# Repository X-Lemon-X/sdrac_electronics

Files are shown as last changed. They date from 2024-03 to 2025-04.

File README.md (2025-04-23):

 
# SDRAC electronic design
This repository contains the psb schematics and designs of the SDRAC board.

## SDRACboard
- Supply voltage 12-48V (9-55V)
- the board has a 5V/2A on board regualator, to power the board and peripherals
- USB-C for programming and reading data
- ST-wire pins for programming and debugging
- 3 bit hardware address CID0, CID1, CID2
- 6 pin JS connector for IO-appliacitons, with analog, UART, Timers, 5V and GND
- 2x 4 pin Molex connectors for CAN bus
- 2x 6 pin Molex connectors for I2C magnetic encoder
- 2x 2 pin Molex connectors for external temperature sensors (ntc termistors)
- 1x 4 pin Molex connector for stepper motor
- 1x 4 pin connector for external steper motor driver
- 1x Screw terminal for external steper motor driver power
- XT30-M, XT30-F  connectors for input and output power

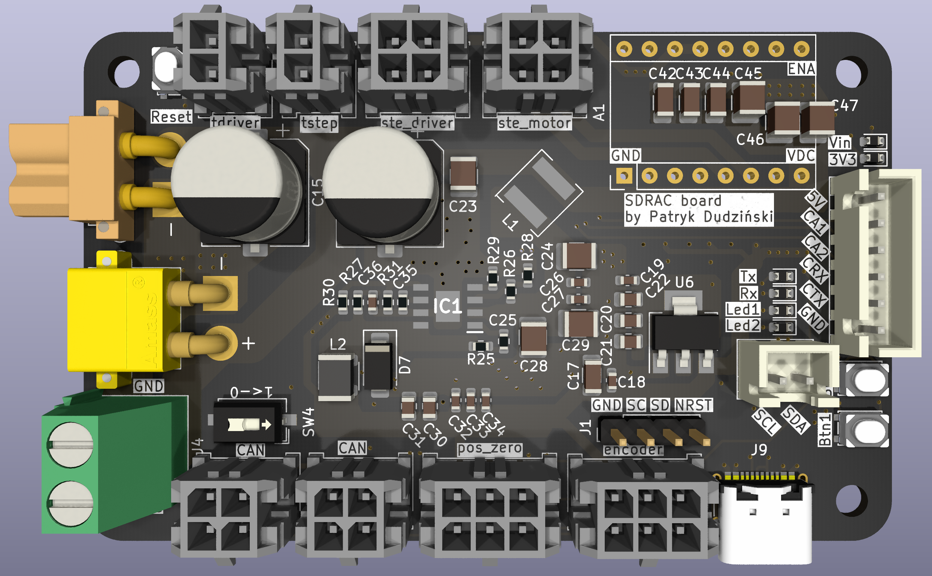
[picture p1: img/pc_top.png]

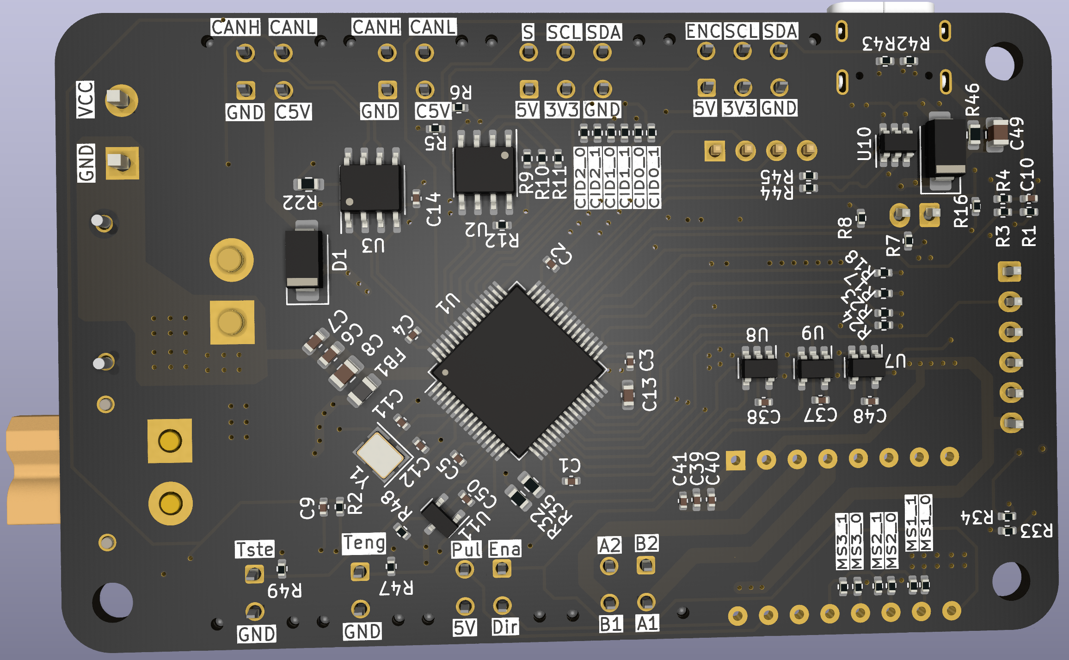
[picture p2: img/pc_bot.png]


## Schematics
The schematics are made in KiCad.

## Assembly
Manual assembly takes about 2 hours, with stemple and hot air station.

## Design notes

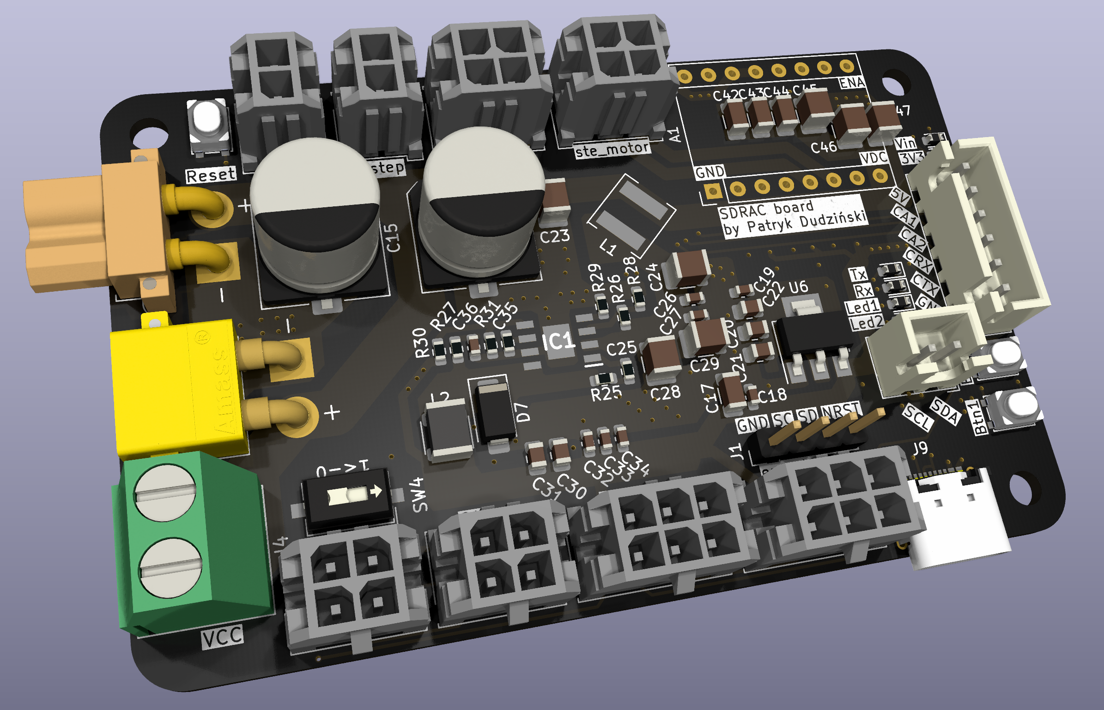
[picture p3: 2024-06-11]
img/front.png

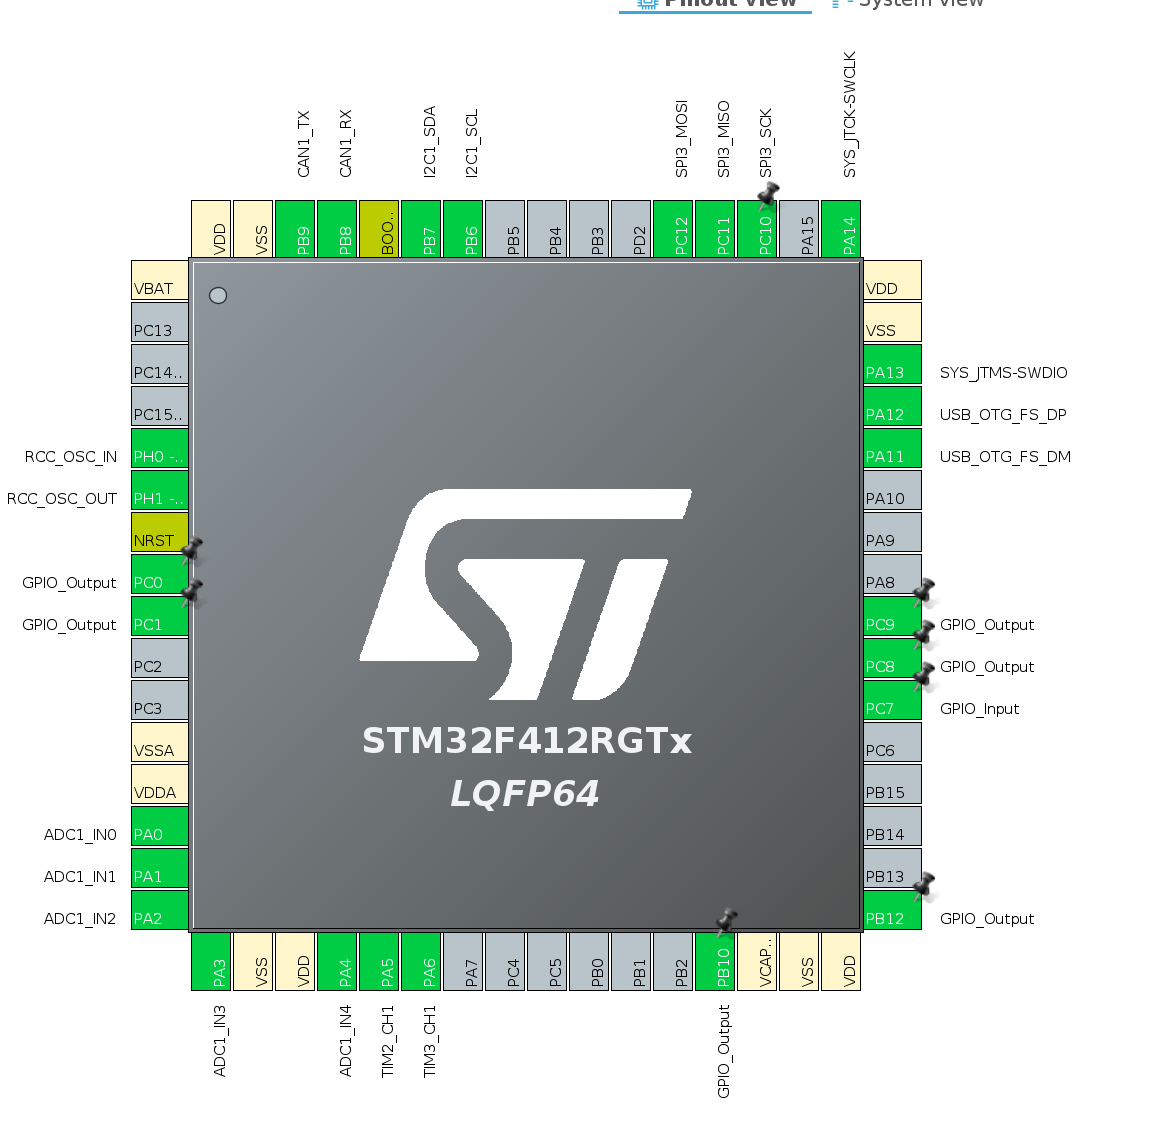
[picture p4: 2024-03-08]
datasheets/stm_cube_uc_image.png

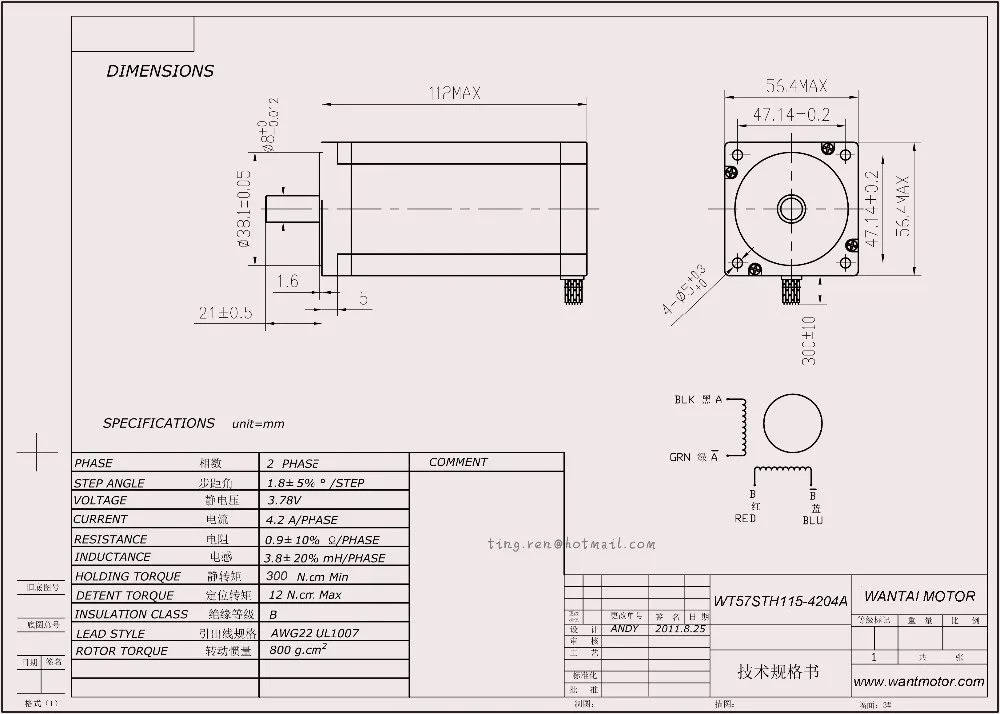
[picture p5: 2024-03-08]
datasheets/steper_motor_big.webp

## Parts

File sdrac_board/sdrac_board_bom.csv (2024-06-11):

Id | Designator | Footprint | Quantity | Designation | Supplier and ref
1 | R28 | R_0603_1608Metric | 1 | 86.6k
2 | U4,U5 | Molex_Micro-Fit_3.0_43045-0412_2x02_P3.00mm_Vertical | 2 | CAN
3 | R29 | R_0603_1608Metric | 1 | 60.4k
4 | U6 | SOT-223-3_TabPin2 | 1 | AZ1117-3.3
5 | J6 | AMASS_XT30PW-F_1x02_P2.50mm_Horizontal | 1 | Conn_01x02_Female
6 | J8 | Molex_Micro-Fit_3.0_43045-0412_2x02_P3.00mm_Vertical | 1 | STEPER_DRIVER_MOTOR_OUT
7 | SW4 | SW_DIP_SPSTx01_Slide_6.7x4.1mm_W6.73mm_P2.54mm_LowProfile_JPin | 1 | SW_DIP_x01
8 | D6 | D_0603_1608Metric | 1 | LED_TXD
9 | C16,C15 | CP_Elec_10x10.5 | 2 | 47u
10 | J5 | AMASS_XT30PW-M_1x02_P2.50mm_Horizontal | 1 | Conn_01x02_Male
11 | R30,R32 | R_0603_1608Metric | 2 | 43k
12 | C35 | R_0603_1608Metric | 1 | 0.033u
13 | C33,C18,C26,C32,C19 | C_0603_1608Metric | 5 | 100n
14 | C43,C44 | C_1206_3216Metric | 2 | 100n
15 | C47,C23,C29,C28,C46,C24,C45 | C_1210_3225Metric | 7 | 10u
16 | J12 | Molex_Micro-Fit_3.0_43045-0612_2x03_P3.00mm_Vertical | 1 | Pos_zero_sens
17 | D3 | D_0603_1608Metric | 1 | USR_LED1
18 | C25 | R_0603_1608Metric | 1 | 100n
19 | C17 | C_1206_3216Metric | 1 | 10u
20 | C34,C27 | C_0603_1608Metric | 2 | 1n
21 | SW2 | SW_SPST_PTS810 | 1 | NRST
22 | SW1 | SW_SPST_PTS810 | 1 | BOOT0
23 | C30,C21,C31,C22,C20,C8 | C_0805_2012Metric | 6 | 10u
24 | R26 | R_0603_1608Metric | 1 | 430k
25 | R31 | R_0603_1608Metric | 1 | 7.5k
26 | D7 | D_SMA | 1 | SS34
27 | SW3 | SW_SPST_PTS810 | 1 | USR_BTN
28 | H1,H2,H3 | MountingHole_3.2mm_M3_ISO7380 | 3 | MountingHole
29 | R27,R25 | R_0603_1608Metric | 2 | 5.1
30 | J11 | Molex_Micro-Fit_3.0_43045-0612_2x03_P3.00mm_Vertical | 1 | Mag_enc
31 | IC1 | SOIC127P600X170-9N | 1 | LMR16030PDDA
32 | J1 | PinHeader_1x04_P2.54mm_Vertical | 1 | SWD
33 | J9 | USB_C_Receptacle_G-Switch_GT-USB-7010ASV | 1 | USB_C_Receptacle_USB2.0
34 | J7 | Molex_Micro-Fit_3.0_43045-0412_2x02_P3.00mm_Vertical | 1 | STEPER_DRIVER_CONTROL
35 | L1 | L_6.3x6.3_H3 | 1 | 22u
36 | J3 | JST_XH_B6B-XH-A_1x06_P2.50mm_Vertical | 1 | INOUT
37 | D9 | D_0603_1608Metric | 1 | LV_PWR
38 | D8 | D_0603_1608Metric | 1 | HV_PWR
39 | D4 | D_0603_1608Metric | 1 | USR_LED2
40 | L2 | L_1812_4532Metric | 1 | 12u
41 | J4 | TerminalBlock_Phoenix_MKDS-1,5-2_1x02_P5.00mm_Horizontal | 1 | STEPER DRIVER VCC
42 | A1 | Pololu_Breakout-16_15.2x20.3mm | 1 | STEPER_MOTOR_BREAKOUT
43 | J10,J13 | Molex_Micro-Fit_3.0_43045-0212_2x01_P3.00mm_Vertical | 2 | Conn_01x02
44 | C36 | C_0603_1608Metric | 1 | 100p
45 | D5 | D_0603_1608Metric | 1 | LED_RXD
46 | C42 | C_1206_3216Metric | 1 | 1n
47 | J2 | JST_XH_B2B-XH-A_1x02_P2.50mm_Vertical | 1 | SYNCHRONIZER
48 | U3 | SOIC-8_3.9x4.9mm_P1.27mm | 1 | SN65HVD232
49 | R48,R47,R49 | R_0402_1005Metric | 3 | 100k
50 | R6,R8,R7,R5 | R_0402_1005Metric | 4 | 4k7
51 | C39,C40 | C_0402_1005Metric_Pad0.74x0.62mm_HandSolder | 2 | 100n
52 | U7,U9,U8 | SOT-23-5 | 3 | SN74LV1T34DBV
53 | U11 | SOT-23 | 1 | MCP9700AT-ETT
54 | R3,R23,R34,R1,R17,R24,R18 | R_0402_1005Metric | 7 | 1k
55 | R2,R4,R16,R19,R36,R13,R41,R20,R10,R15,R40,R39,R11,R12,R14,R33,R37,R9,R21,R38 | R_0402_1005Metric | 20 | 10k
56 | R45,R44 | R_0402_1005Metric | 2 | 22R
57 | R22 | R_0603_1608Metric | 1 | 120R
58 | U1 | LQFP-64_10x10mm_P0.5mm | 1 | STM32F412RGT6
59 | R43,R42 | R_0402_1005Metric | 2 | 5k1
60 | C2,C37,C9,C1,C50,C4,C14,C48,C5,C3,C38 | C_0402_1005Metric | 11 | 100n
61 | D2,D1 | D_SMA | 2 | D_Schottky
62 | R46 | R_0603_1608Metric | 1 | 33k
63 | C11,C12 | C_0402_1005Metric | 2 | 16p
64 | C6 | C_0603_1608Metric | 1 | 1u
65 | C49 | C_0805_2012Metric | 1 | 10n
66 | R35 | R_0603_1608Metric | 1 | 1k
67 | C41 | C_0402_1005Metric | 1 | 1n
68 | C7 | C_0603_1608Metric | 1 | 4.7u
69 | U10 | SOT-23-6 | 1 | USBLC6-2SC6
70 | C10 | C_0402_1005Metric | 1 | 4.7u
71 | C13 | C_0603_1608Metric | 1 | 2.2u
72 | Y1 | Crystal_SMD_3225-4Pin_3.2x2.5mm | 1 | 16MHz
73 | U2 | SOIC-8_3.9x4.9mm_P1.27mm | 1 | FM24CL16B
74 | FB1 | L_0805_2012Metric | 1 | FerriteBead

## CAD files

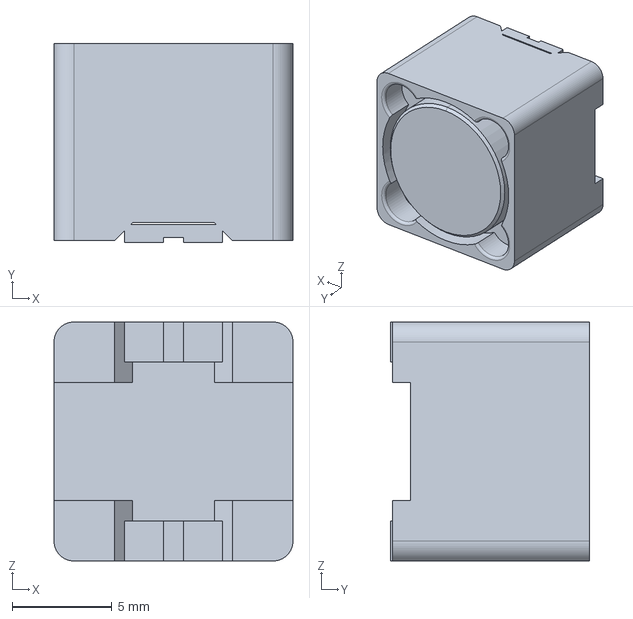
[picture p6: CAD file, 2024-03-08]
sdrac_board/3D models/SRR1210-471M.stp
12.0 x 10.0 x 12.0 mm

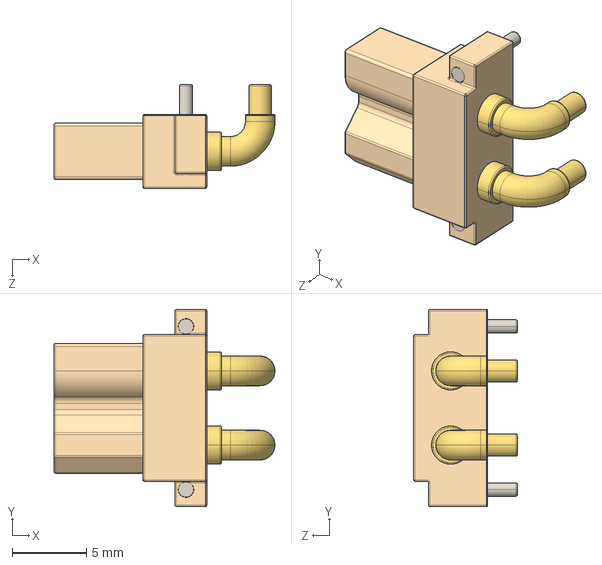
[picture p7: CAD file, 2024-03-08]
sdrac_board/3D models/XT30PW-F.STEP
14.9 x 13.3 x 7.00 mm

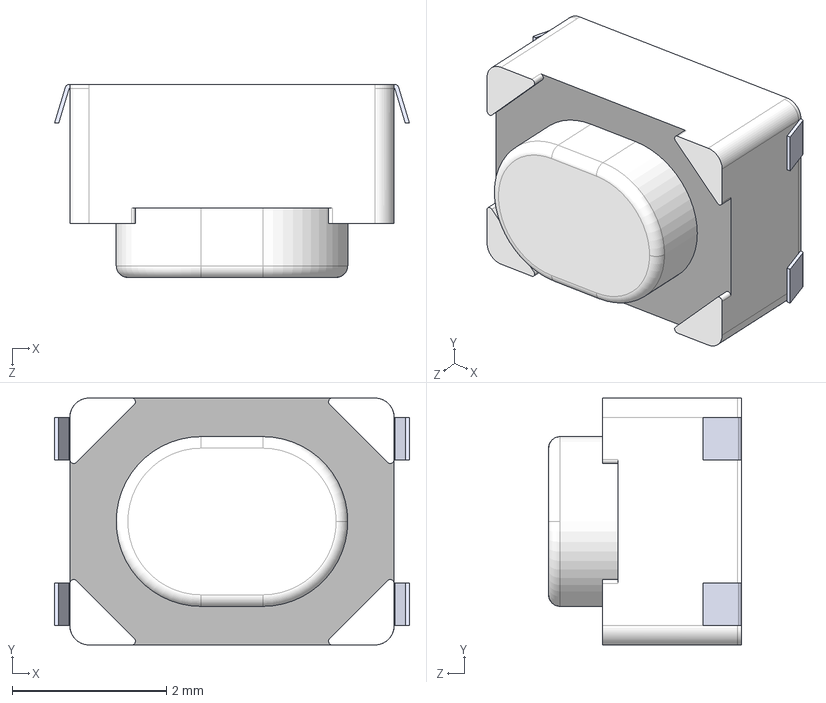
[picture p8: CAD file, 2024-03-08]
sdrac_board/3D models/PTS810 Series SJS 250.STEP
4.60 x 3.20 x 2.50 mm

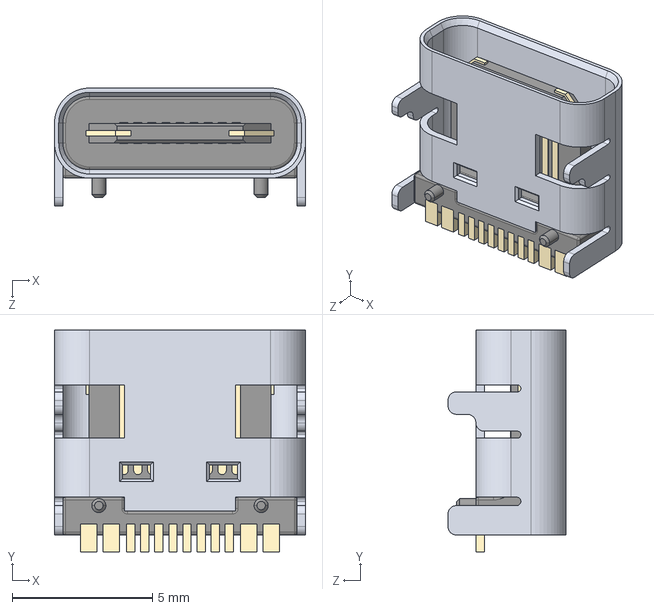
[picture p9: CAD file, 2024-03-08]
sdrac_board/3D models/USB Type C Port (SMD Type).STEP
8.94 x 7.90 x 4.20 mm

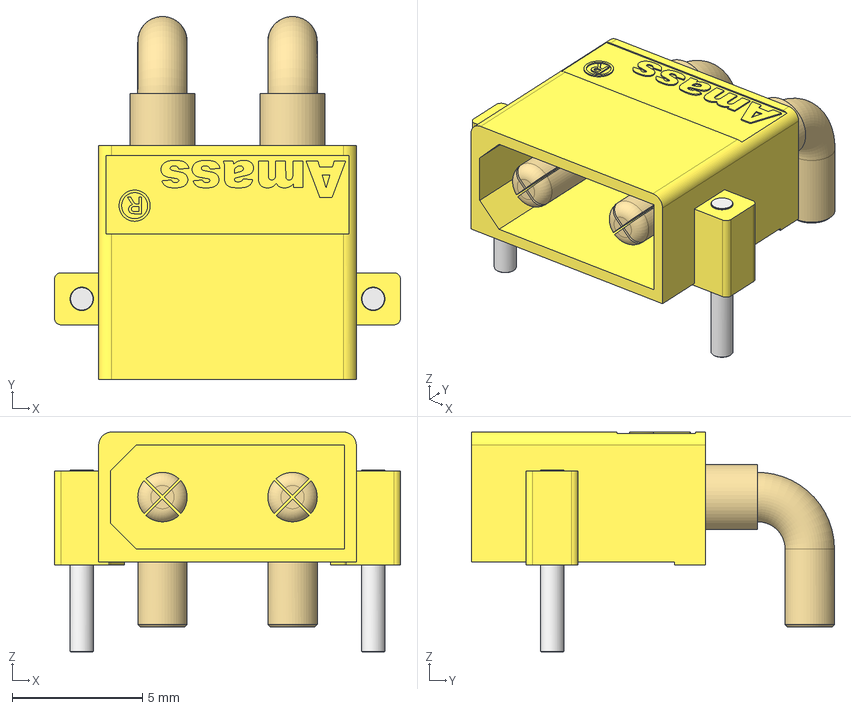
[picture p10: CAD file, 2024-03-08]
sdrac_board/3D models/Amass_XT30PW-M_pcb solder.stp
13.3 x 13.9 x 8.45 mm

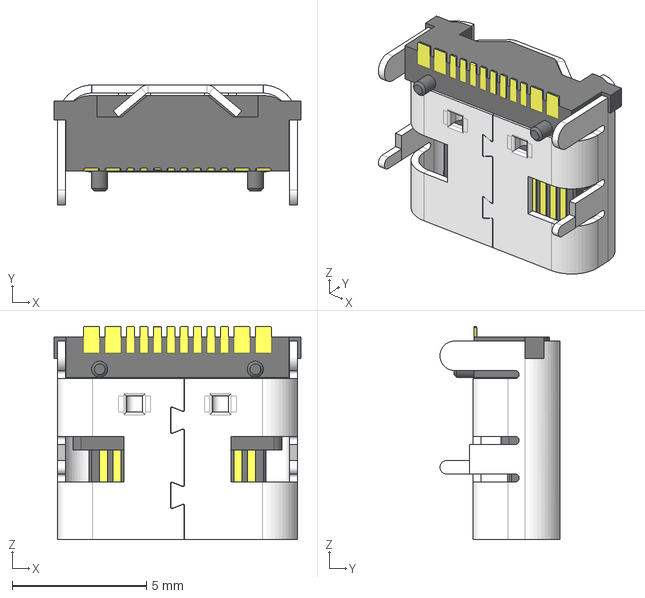
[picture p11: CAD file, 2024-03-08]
sdrac_board/3D models/USB_type_C_smd_12p.stp
9.20 x 4.47 x 7.95 mm

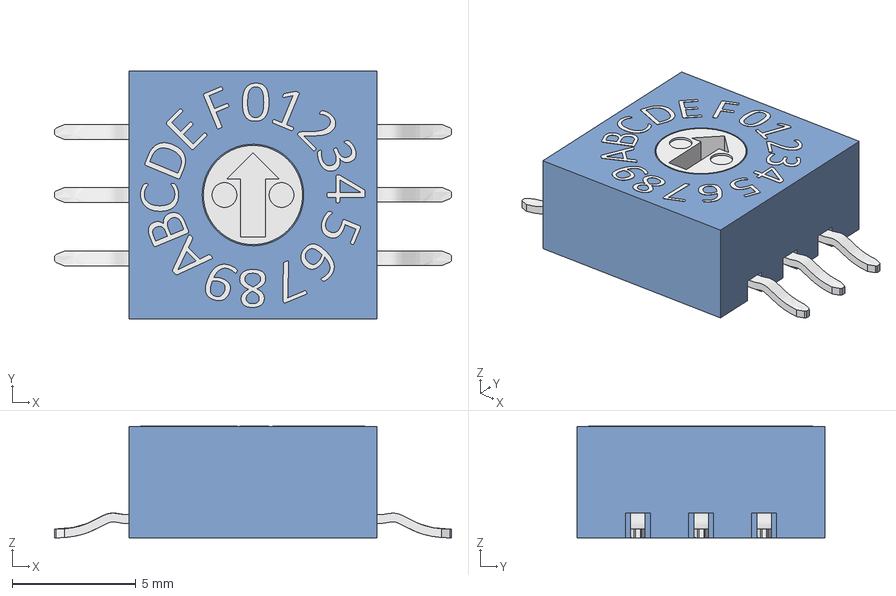
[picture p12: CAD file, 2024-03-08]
sdrac_board/3D models/8421C-smt.stp
16.0 x 10.0 x 4.51 mm
Main
ExtrudeA
Circle
Rotary
Leg4
LegC1
Leg1
ExtrudeB
ExtrudeC
ExtrudeD
ExtrudeF
ExtrudeE
ExtrudePin8
ExtrudePin1
ExtrudePinC1
ExtrudePinC2
ExtrudePin4
ExtrudePin2
Leg2
LegC2
Leg8

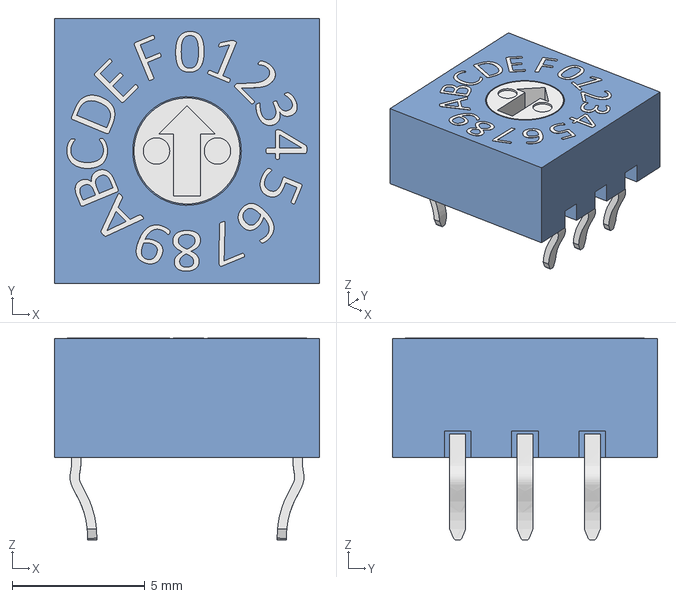
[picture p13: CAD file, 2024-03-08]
sdrac_board/3D models/8421C.step
10.0 x 10.0 x 7.61 mm

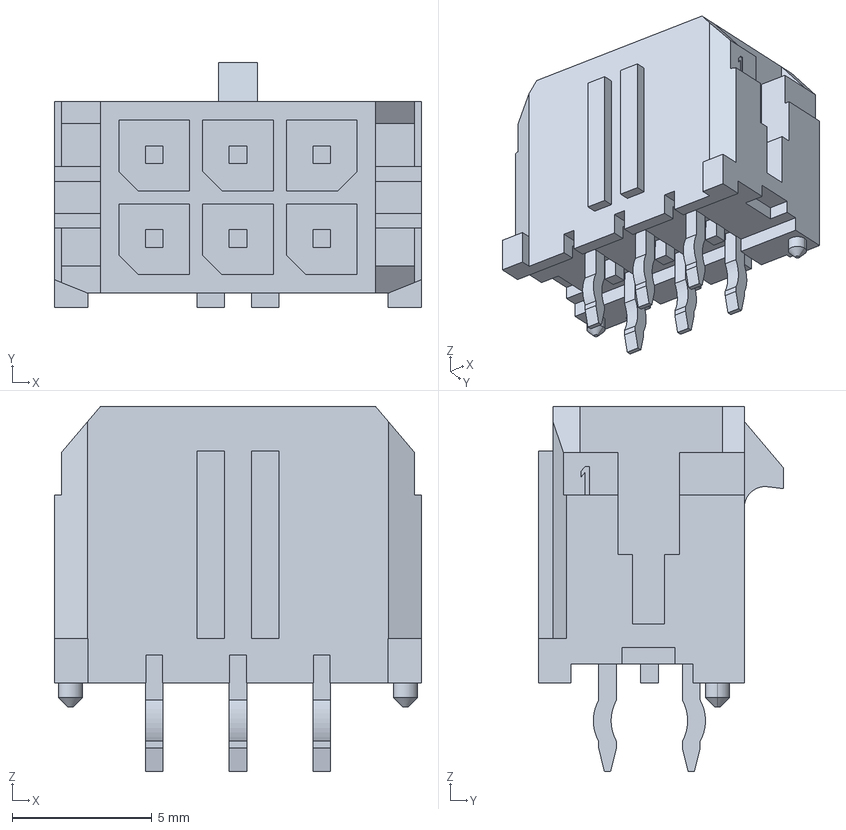
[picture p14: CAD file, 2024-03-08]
sdrac_board/3D models/430450612.stp
13.2 x 8.77 x 13.1 mm

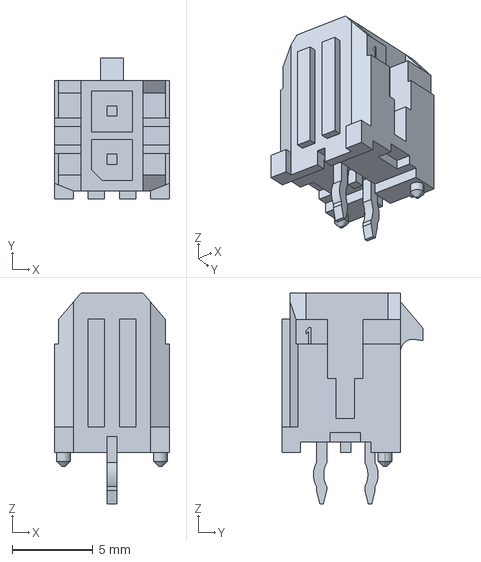
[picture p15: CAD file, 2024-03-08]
sdrac_board/3D models/430450212.stp
7.15 x 8.77 x 13.1 mm

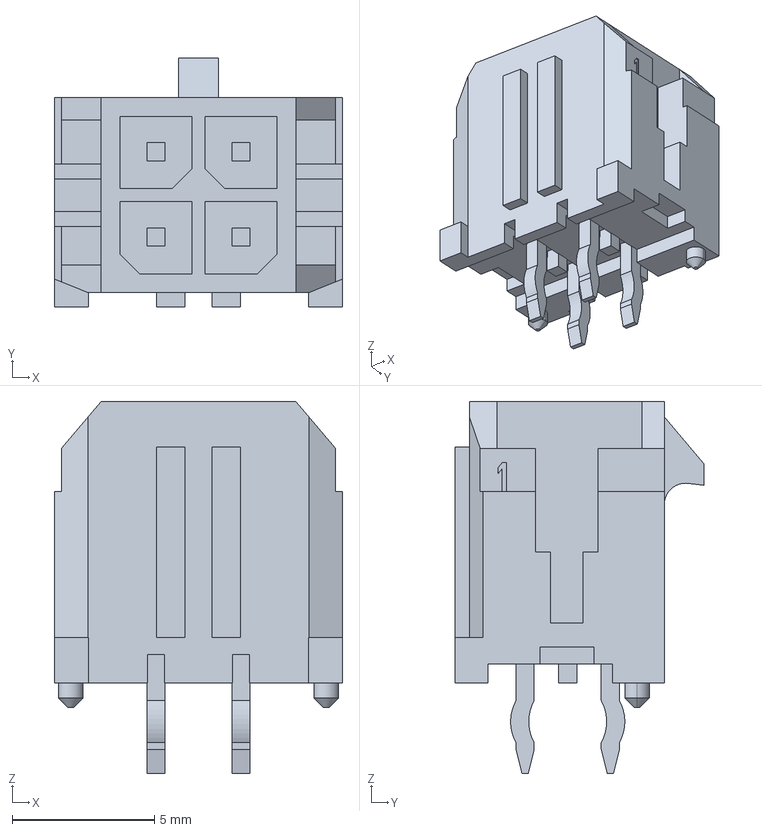
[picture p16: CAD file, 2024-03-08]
sdrac_board/3D models/430450412.stp
10.2 x 8.77 x 13.1 mm

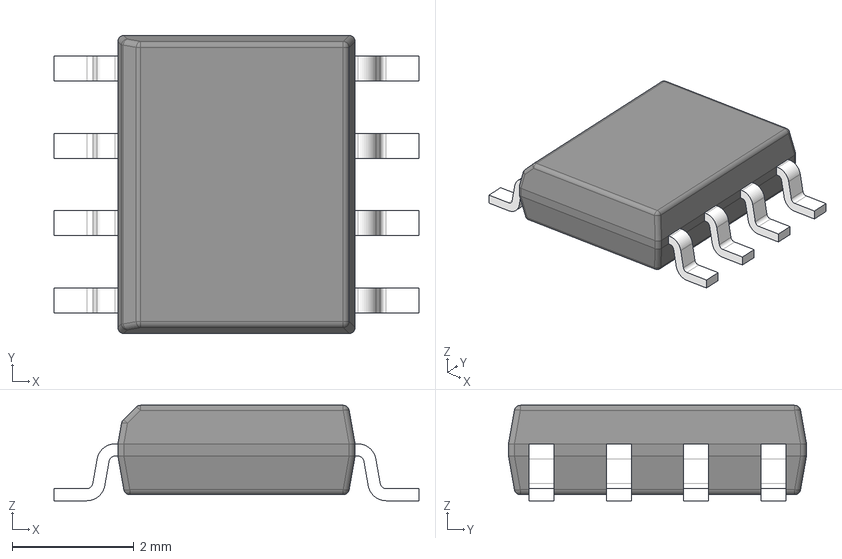
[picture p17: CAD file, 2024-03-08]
sdrac_board/3D models/LMR16030SDDAR.stp
6.00 x 4.90 x 1.57 mm
BODY-SO
LEAD-SO x 8
THERMALPAD-SO

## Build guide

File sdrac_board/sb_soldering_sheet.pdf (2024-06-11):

sdrac_board-all-pos

Ref | Val | Side | Done | Ref | Val | Side | Done
C1 | 100n | bottom | | A1 | SM_BREAKOUT | top
C2 | 100n | bottom | | C16 | 47u | top
C3 | 100n | bottom | | C17 | 10u | top
C4 | 100n | bottom | | C18 | 100n | top
C5 | 100n | bottom | | C19 | 100n | top
C6 | 1u | bottom | | C20 | 10u | top
C7 | 4.7u | bottom | | C21 | 10u | top
C8 | 10u | bottom | | C22 | 10u | top
C9 | 100n | bottom | | C23 | 10u | top
C10 | 4.7u | bottom | | C24 | 10u | top
C11 | 16p | bottom | | C25 | 100n | top
C12 | 16p | bottom | | C26 | 100n | top
C13 | 2.2u | bottom | | C27 | 1n | top
C14 | 100n | bottom | | C30 | 10u | top
C37 | 100n | bottom | | C31 | 10u | top
C38 | 100n | bottom | | C32 | 100n | top
C39 | 100n | bottom | | C33 | 100n | top
C40 | 100n | bottom | | C34 | 1n | top
C41 | 1n | bottom | | C36 | 100p | top
C48 | 100n | bottom | | C42 | 1n | top
C49 | 10n | bottom | | C43 | 100n | top
C50 | 100n | bottom | | C44 | 100n | top
D1 | D_Schottky | bottom | | D3 | USR_LED1 | top
D2 | D_Schottky | bottom | | D4 | USR_LED2 | top
FB1 | FerriteBead | bottom | | D5 | LED_RXD | top
R1 | 1k | bottom | | D6 | LED_TXD | top
R2 | 10k | bottom | | D7 | SS34 | top
R3 | 1k | bottom | | D8 | HV_PWR | top
R4 | 10k | bottom | | D9 | LV_PWR | top
R5 | 4k7 | bottom | | H1 | MountingHole | top
R6 | 4k7 | bottom | | H2 | MountingHole | top
R7 | 4k7 | bottom | | H3 | MountingHole | top
R8 | 4k7 | bottom | | IC1 | LMR16030PDDA | top
R9 | 10k | bottom | | J1 | SWD | top
R10 | 10k | bottom | | J2 | SYNCHRONIZER | top
R11 | 10k | bottom | | J3 | INOUT | top
R12 | 10k | bottom | | J4 | STEPER DRIVER VCC | top
R13 | 10k | bottom | | J5 | Conn_01x02_Male | top
R14 | 10k | bottom | | J6 | Conn_01x02_Female | top
R15 | 10k | bottom | | J7 | S_D_CONTROL | top
R16 | 10k | bottom | | J8 | SD_MOTOR_OUT | top
R17 | 1k | bottom | | J9 | USB_C_USB2.0 | top
R18 | 1k | bottom | | J10 | Conn_01x02 | top
R19 | 10k | bottom | | J11 | Mag_enc | top
R20 | 10k | bottom | | J12 | Pos_zero_sens | top
R21 | 10k | bottom | | J13 | Conn_01x02 | top
R22 | 120R | bottom | | L1 | 22u | top
R23 | 1k | bottom | | L2 | 12u | top
R24 | 1k | bottom | | R25 | 5.1 | top
R32 | 43k | bottom | | R26 | 430k | top
R33 | 10k | bottom | | R27 | 5.1 | top
R34 | 1k | bottom | | R28 | 86.6k | top

sdrac_board-all-pos

R35 | 1k | bottom | R29 | 60.4k | top
R36 | 10k | bottom | R30 | 43k | top
R37 | 10k | bottom | R31 | 7.5k | top
R38 | 10k | bottom | SW1 | BOOT0 | top
R39 | 10k | bottom | SW2 | NRST | top
R40 | 10k | bottom | SW3 | USR_BTN | top
R41 | 10k | bottom | SW4 | SW_DIP_x01 | top
R42 | 5k1 | bottom | U4 | CAN | top
R43 | 5k1 | bottom | U5 | CAN | top
R44 | 22R | bottom | U6 | AZ1117-3.3 | top
R45 | 22R | bottom
R46 | 33k | bottom
R47 | 100k | bottom
R48 | 100k | bottom
R49 | 100k | bottom
U1 | STM32F412RGT6 | bottom
U2 | FM24CL16B | bottom
U3 | SN65HVD232 | bottom
U7 | SN74LV1T34DBV | bottom
U8 | SN74LV1T34DBV | bottom
U9 | SN74LV1T34DBV | bottom
U10 | USBLC6-2SC6 | bottom
U11 | MCP9700AT-ETT | bottom
Y1 | 16MHz | bottom

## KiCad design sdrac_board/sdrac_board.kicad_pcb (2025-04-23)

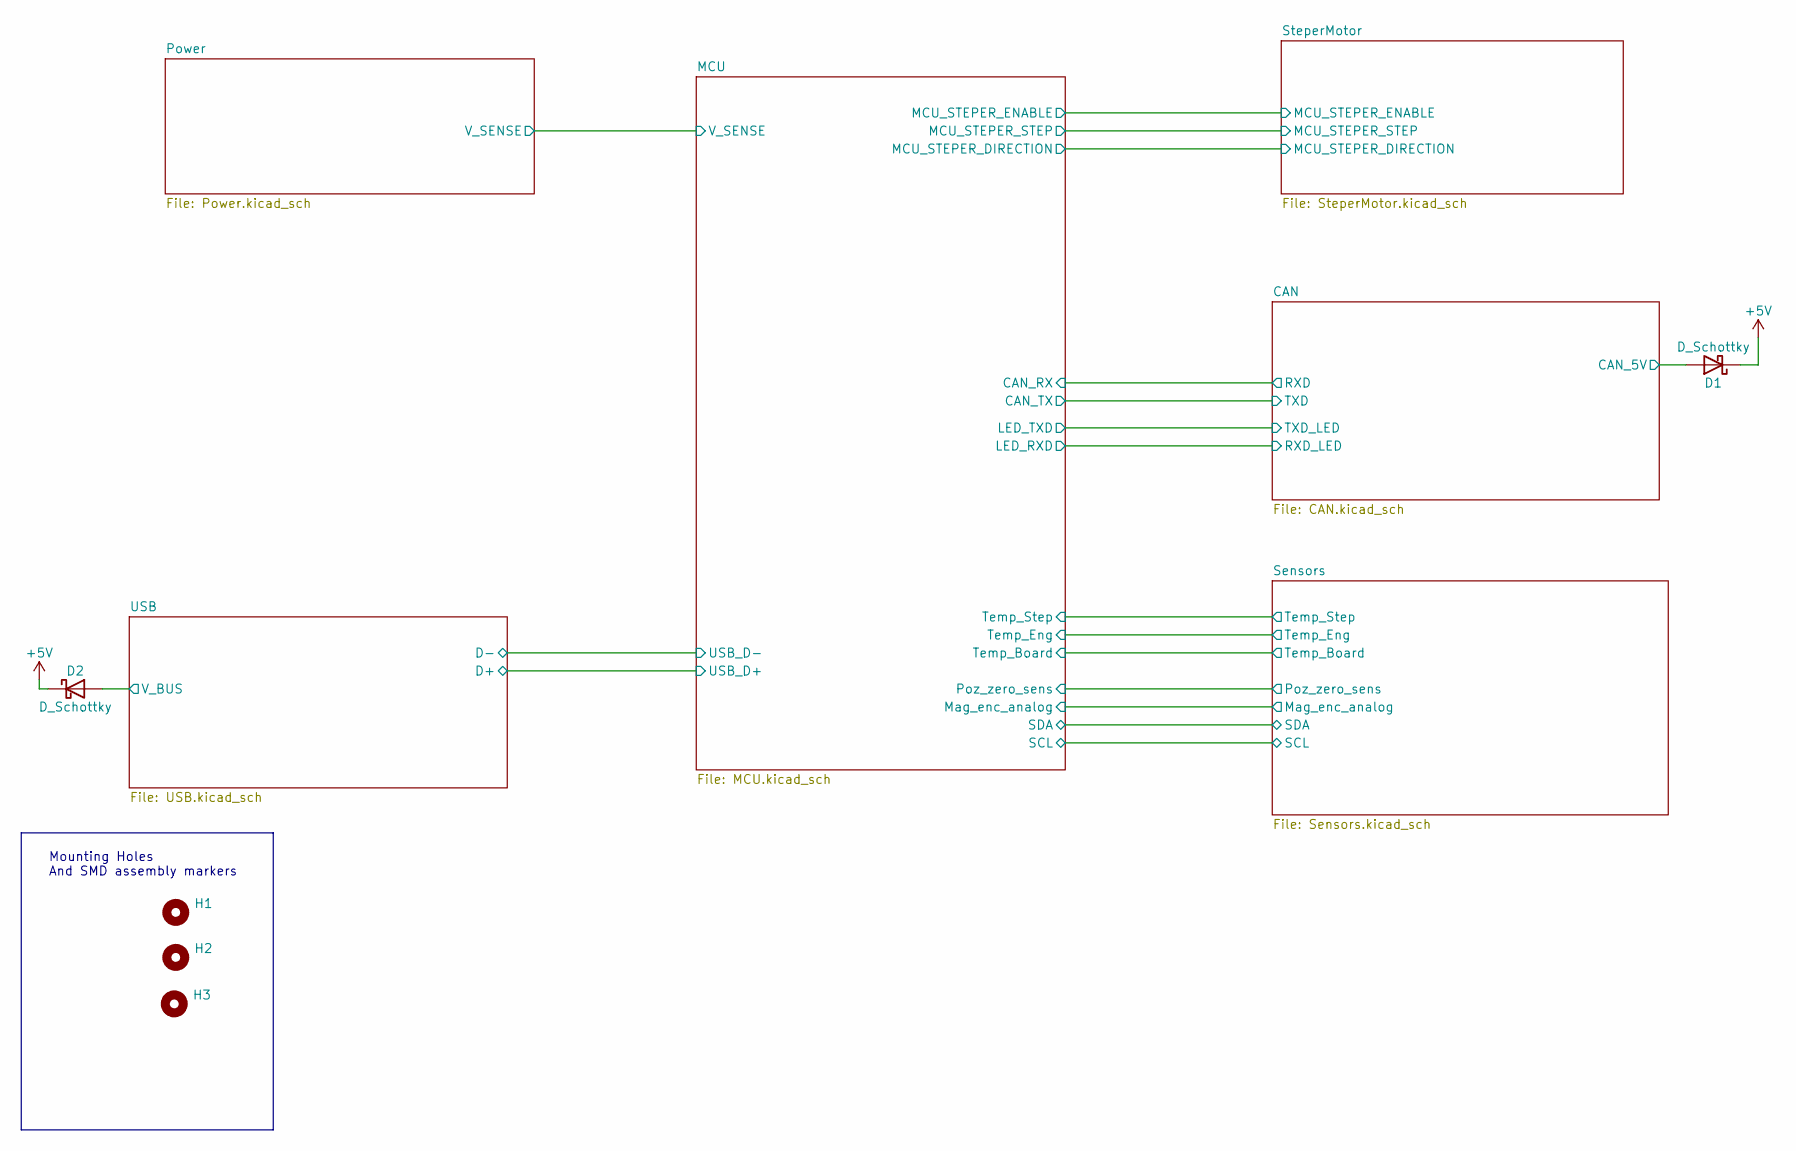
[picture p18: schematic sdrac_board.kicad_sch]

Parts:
D1, D2: D_Schottky; D_SMA
H1, H2, H3: MountingHole; MountingHole_3.2mm_M3_ISO7380

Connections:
+5V: D1.1 (K), D2.1 (K); also elsewhere on the board
/CAN/CAN_5V: D1.2 (A); also elsewhere on the board
/USB/V_BUS: D2.2 (A); also elsewhere on the board

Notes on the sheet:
Mounting Holes And SMD assembly markers

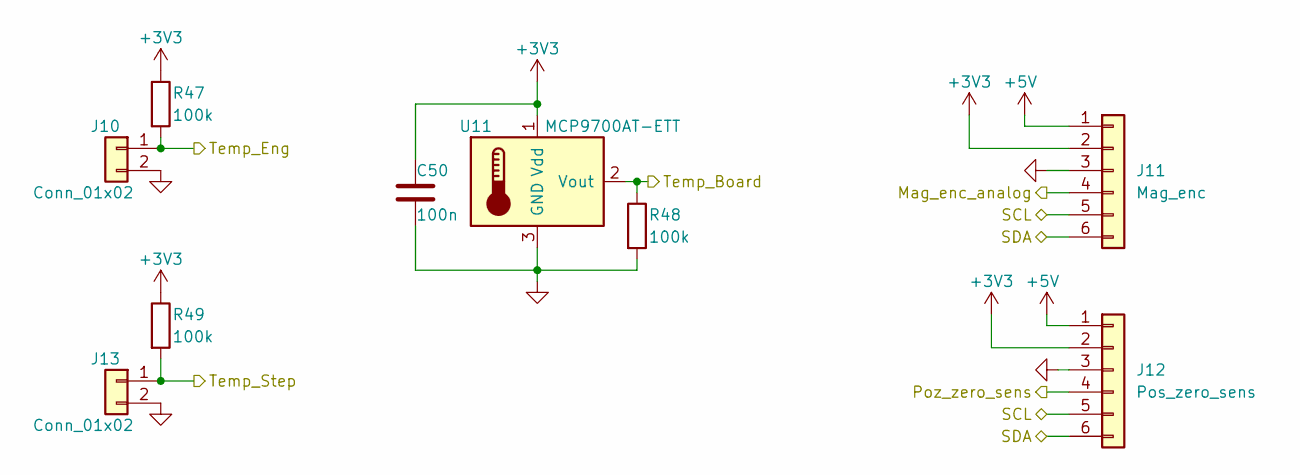
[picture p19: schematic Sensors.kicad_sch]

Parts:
C50: 100n; C_0402_1005Metric
J10, J13: Conn_01x02; Molex_Micro-Fit_3.0_43045-0212_2x01_P3.00mm_Vertical
J11: Mag_enc; Molex_Micro-Fit_3.0_43045-0612_2x03_P3.00mm_Vertical
J12: Pos_zero_sens; Molex_Micro-Fit_3.0_43045-0612_2x03_P3.00mm_Vertical
R47, R48, R49: 100k; R_0402_1005Metric
U11: MCP9700AT-ETT; SOT-23

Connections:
+3V3: C50.1, J11.2, J12.2, R47.1, R49.1, U11.1 (Vdd); also elsewhere on the board
+5V: J11.1, J12.1; also elsewhere on the board
/MCU/Mag_enc_analog: J11.4; also elsewhere on the board
/MCU/Poz_zero_sens: J12.4; also elsewhere on the board
/MCU/SCL: J11.5, J12.5; also elsewhere on the board
/MCU/SDA: J11.6, J12.6; also elsewhere on the board
/MCU/Temp_Board: R48.1, U11.2 (Vout); also elsewhere on the board
/MCU/Temp_Eng: J10.1, R47.2; also elsewhere on the board
/MCU/Temp_Step: J13.1, R49.2; also elsewhere on the board
GND: C50.2, J10.2, J11.3, J12.3, J13.2, R48.2, U11.3 (GND); also elsewhere on the board

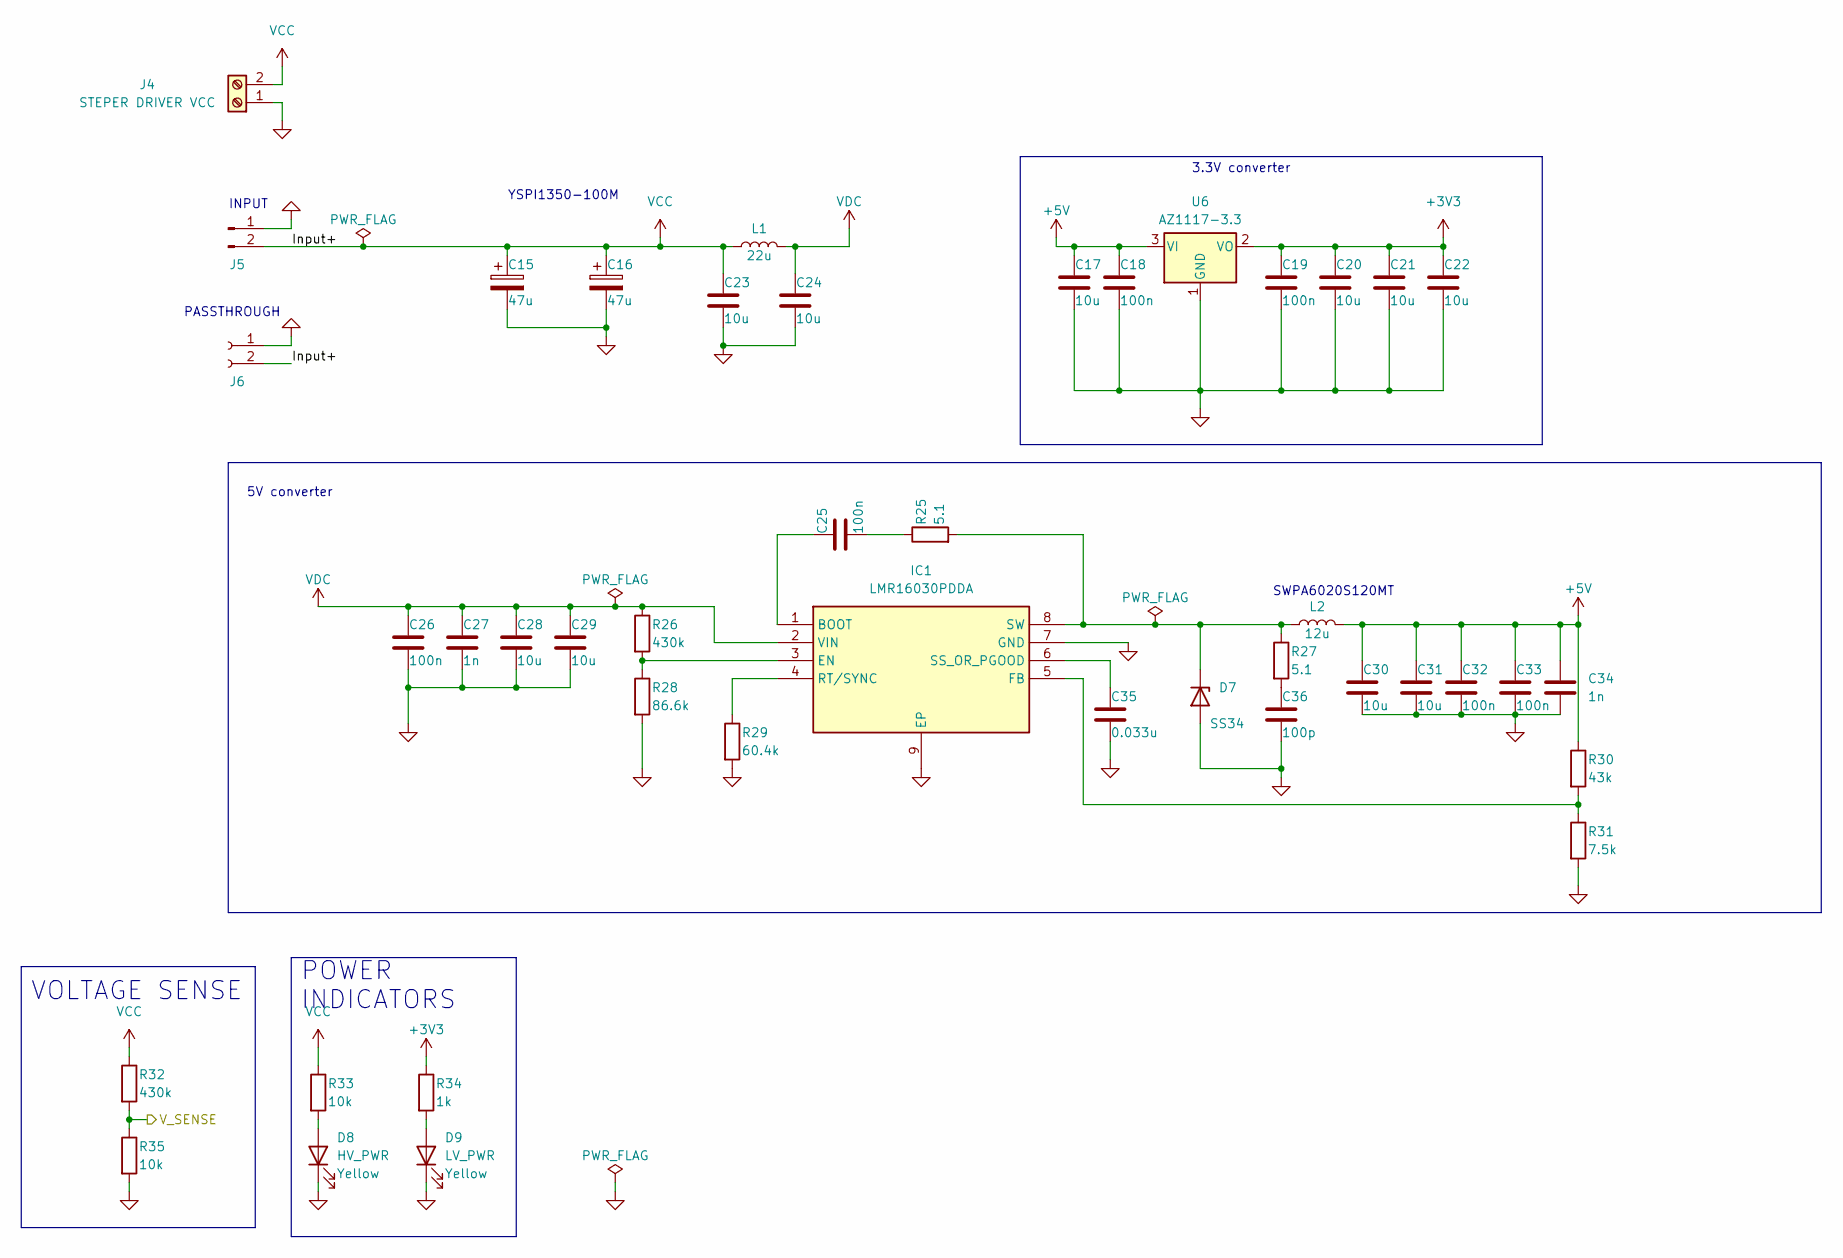
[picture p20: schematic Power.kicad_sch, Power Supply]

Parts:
C15, C16: 47u; CP_Elec_10x10.5
C17: 10u; C_1206_3216Metric
C18, C19, C26, C32, C33: 100n; C_0603_1608Metric
C20, C21, C22, C30, C31: 10u; C_0805_2012Metric
C23, C24, C28, C29: 10u; C_1210_3225Metric
C25: 100n; R_0603_1608Metric
C27, C34: 1n; C_0603_1608Metric
C35: 0.033u; R_0603_1608Metric
C36: 100p; C_0603_1608Metric
D7: SS34; D_SMA
D8: HV_PWR; D_0603_1608Metric
D9: LV_PWR; D_0603_1608Metric
IC1: LMR16030PDDA; SOIC127P600X170-9N; Manufacturer_Part_Number LMR16030PDDA; Mouser Part Number 595-LMR16030PDDA
J4: STEPER DRIVER VCC; TerminalBlock_Phoenix_MKDS-1,5-2_1x02_P5.00mm_Horizontal
J5: Conn_01x02_Male; AMASS_XT30PW-M_1x02_P2.50mm_Horizontal
J6: Conn_01x02_Female; AMASS_XT30PW-F_1x02_P2.50mm_Horizontal
L1: 22u; L_6.3x6.3_H3
L2: 12u; L_1812_4532Metric
R25, R27: 5.1; R_0603_1608Metric
R26, R32: 430k; R_0603_1608Metric
R28: 86.6k; R_0603_1608Metric
R29: 60.4k; R_0603_1608Metric
R30: 43k; R_0603_1608Metric
R31: 7.5k; R_0603_1608Metric
R33: 10k; R_0402_1005Metric
R34: 1k; R_0402_1005Metric
R35: 10k; R_0603_1608Metric
U6: AZ1117-3.3; SOT-223-3_TabPin2

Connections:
+3V3: C19.1, C20.1, C21.1, C22.1, R34.1, U6.2 (VO); also elsewhere on the board
+5V: C17.1, C18.1, C30.1, C31.1, C32.1, C33.1, C34.1, L2.2, R30.1, U6.3 (VI); also elsewhere on the board
/MCU/V_SENSE: R32.2, R35.1; also elsewhere on the board
GND: C15.2, C16.2, C17.2, C18.2, C19.2, C20.2, C21.2, C22.2, C23.2, C24.2, C26.2, C27.2, C28.2, C29.2, C30.2, C31.2, C32.2, C33.2, C34.2, C35.2, C36.2, D7.2 (A), D8.1 (K), D9.1 (K), IC1.7 (GND), IC1.9 (EP), J4.1, J5.1, J6.1, R28.2, R29.2, R31.2, R35.2, U6.1 (GND); also elsewhere on the board
unnamed: C25.2, R25.1
unnamed: C36.1, R27.2
unnamed: D7.1 (K), IC1.8 (SW), L2.1, R25.2, R27.1
unnamed: D8.2 (A), R33.2
unnamed: D9.2 (A), R34.2
unnamed: C25.1, IC1.1 (BOOT)
unnamed: IC1.3 (EN), R26.2, R28.1
unnamed: IC1.5 (FB), R30.2, R31.1
unnamed: IC1.4 (RT/SYNC), R29.1
unnamed: C35.1, IC1.6 (SS_OR_PGOOD)
VCC: C15.1, C16.1, C23.1, J4.2, J5.2, J6.2, L1.1, R32.1, R33.1; also elsewhere on the board
VDC: C24.1, C26.1, C27.1, C28.1, C29.1, IC1.2 (VIN), L1.2, R26.1

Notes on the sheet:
POWER INDICATORS
VOLTAGE SENSE
YSPI1350-100M
PASSTHROUGH
SWPA6020S120MT
INPUT
3.3V converter
5V converter

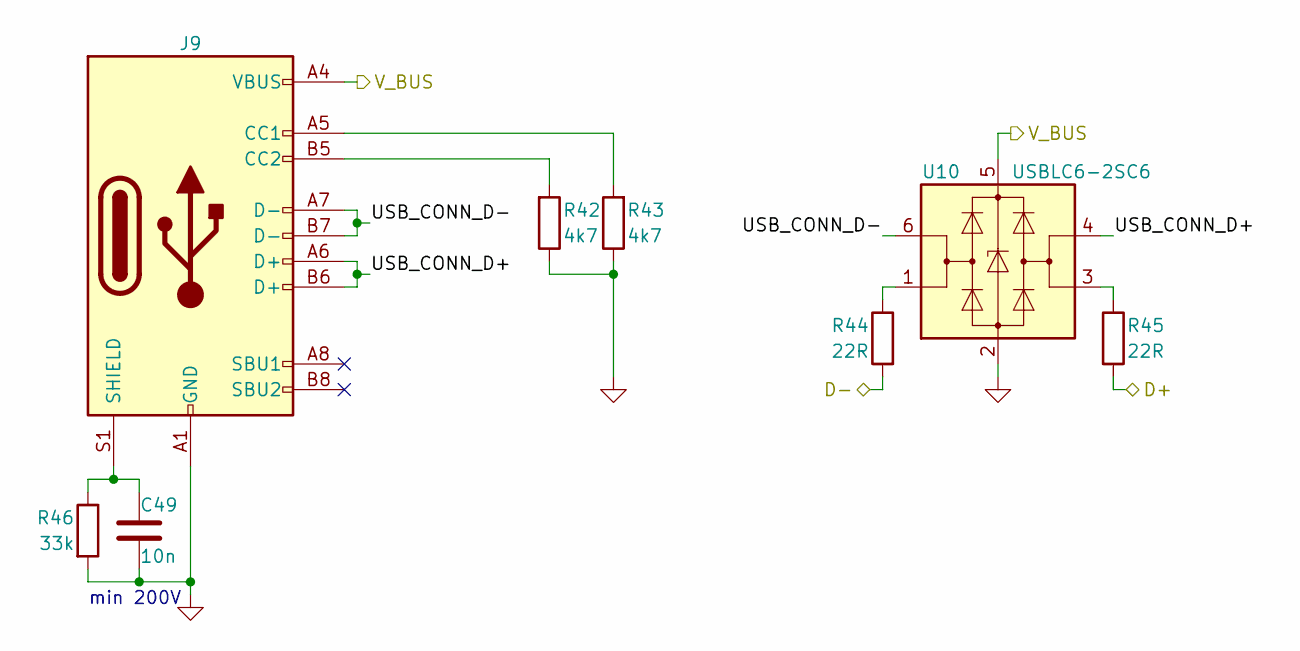
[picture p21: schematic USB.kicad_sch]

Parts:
C49: 10n; C_0805_2012Metric
J9: USB_C_Receptacle_USB2.0; USB_C_Receptacle_G-Switch_GT-USB-7010ASV
R42, R43: 4k7; R_0402_1005Metric
R44, R45: 22R; R_0402_1005Metric
R46: 33k; R_0603_1608Metric
U10: USBLC6-2SC6; SOT-23-6

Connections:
/MCU/USB_D+: R45.2; also elsewhere on the board
/MCU/USB_D-: R44.2; also elsewhere on the board
/USB/USB_CONN_D+: J9.A6 (D+), J9.B6 (D+), U10.4 (I/O2)
/USB/USB_CONN_D-: J9.A7 (D-), J9.B7 (D-), U10.6 (I/O1)
/USB/V_BUS: J9.A4 (VBUS), J9.A9 (VBUS), J9.B4 (VBUS), J9.B9 (VBUS), U10.5 (VBUS); also elsewhere on the board
GND: C49.2, J9.A1 (GND), J9.A12 (GND), J9.B1 (GND), J9.B12 (GND), R42.1, R43.1, R46.2, U10.2 (GND); also elsewhere on the board
unnamed: J9.A5 (CC1), R43.2
unnamed: J9.B5 (CC2), R42.2
unnamed: C49.1, J9.S1 (SHIELD), R46.1
unnamed: R44.1, U10.1 (I/O1)
unnamed: R45.1, U10.3 (I/O2)

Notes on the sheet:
min 200V

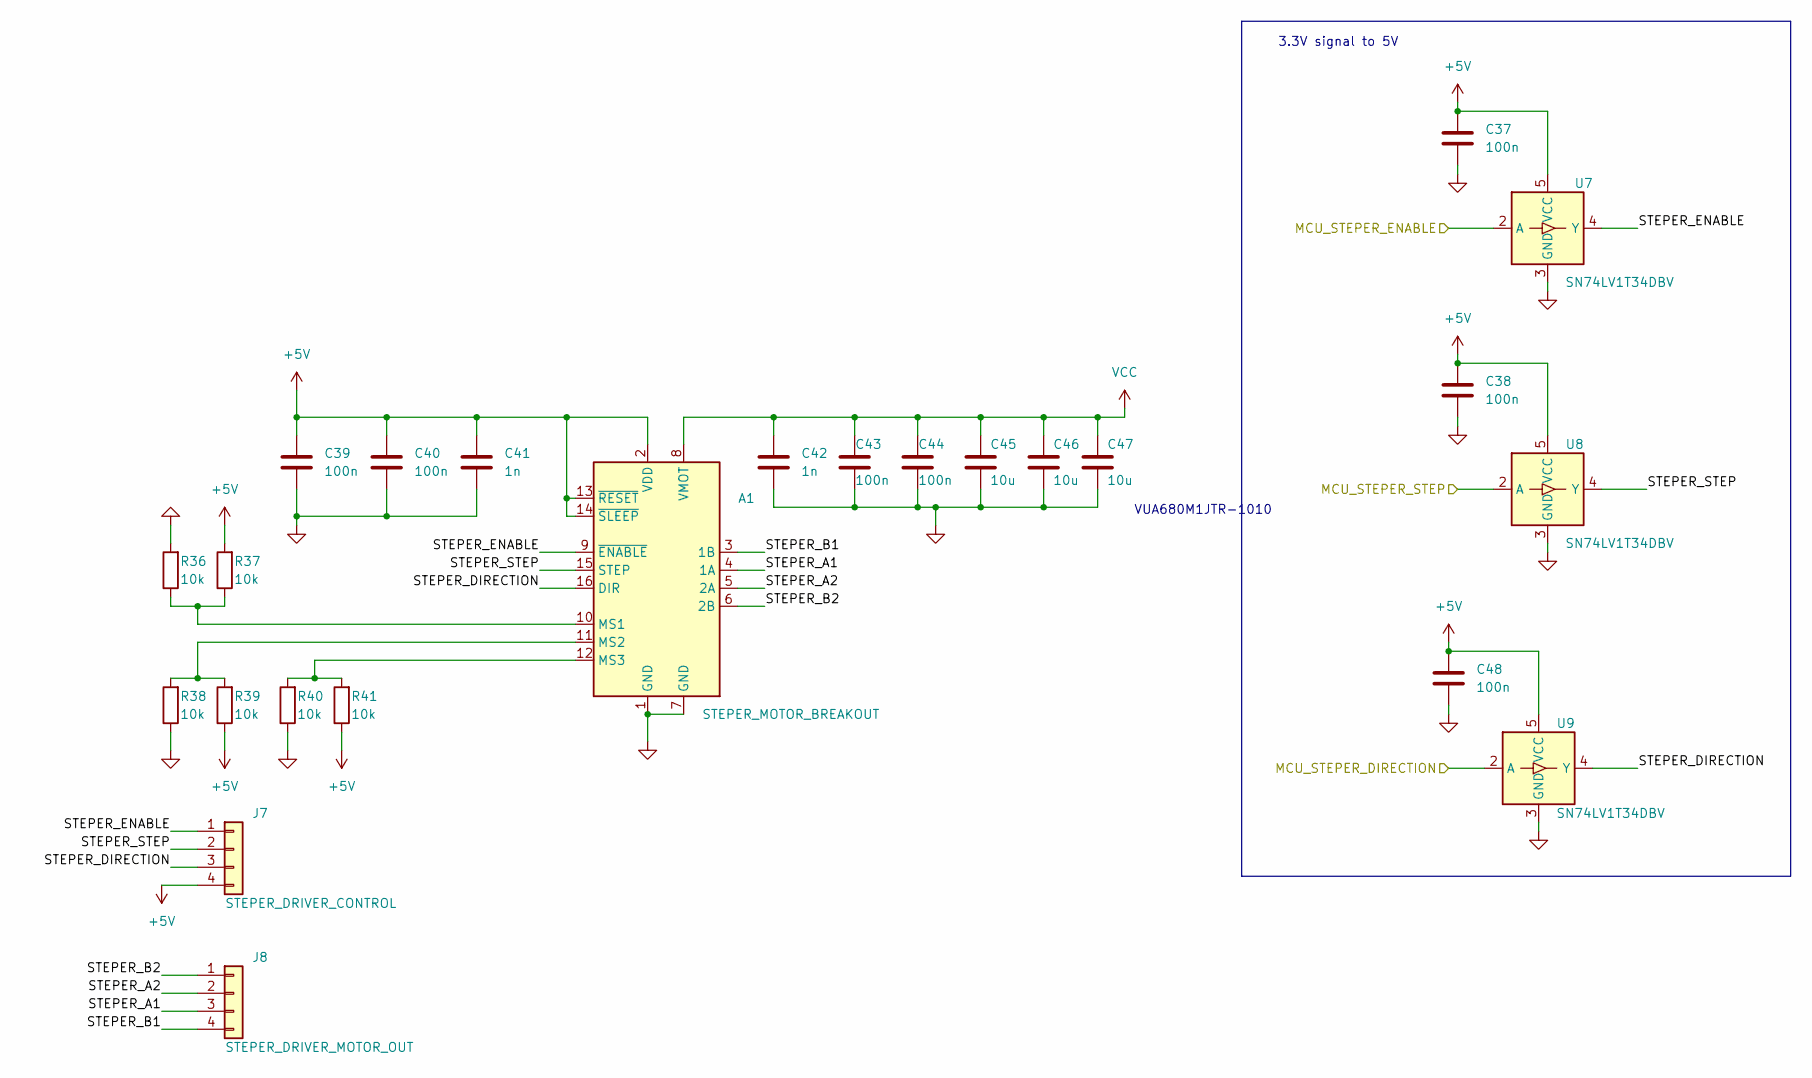
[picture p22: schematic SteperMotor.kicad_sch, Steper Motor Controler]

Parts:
A1: STEPER_MOTOR_BREAKOUT; Pololu_Breakout-16_15.2x20.3mm
C37, C38, C48: 100n; C_0402_1005Metric
C39, C40: 100n; C_0402_1005Metric_Pad0.74x0.62mm_HandSolder
C41: 1n; C_0402_1005Metric
C42: 1n; C_1206_3216Metric
C43, C44: 100n; C_1206_3216Metric
C45, C46, C47: 10u; C_1210_3225Metric
J7: STEPER_DRIVER_CONTROL; Molex_Micro-Fit_3.0_43045-0412_2x02_P3.00mm_Vertical
J8: STEPER_DRIVER_MOTOR_OUT; Molex_Micro-Fit_3.0_43045-0412_2x02_P3.00mm_Vertical
R36, R37, R38, R39, R40, R41: 10k; R_0402_1005Metric
U7, U8, U9: SN74LV1T34DBV; SOT-23-5

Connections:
+5V: A1.2 (VDD), A1.13 (~RESET), A1.14 (~SLEEP), C37.1, C38.1, C39.1, C40.1, C41.1, C48.1, J7.4, R37.2, R39.1, R41.1, U7.5 (VCC), U8.5 (VCC), U9.5 (VCC); also elsewhere on the board
/MCU/MCU_STEPER_DIRECTION: U9.2 (A); also elsewhere on the board
/MCU/MCU_STEPER_ENABLE: U7.2 (A); also elsewhere on the board
/MCU/MCU_STEPER_STEP: U8.2 (A); also elsewhere on the board
/SteperMotor/STEPER_A1: A1.4 (1A), J8.3
/SteperMotor/STEPER_A2: A1.5 (2A), J8.2
/SteperMotor/STEPER_B1: A1.3 (1B), J8.4
/SteperMotor/STEPER_B2: A1.6 (2B), J8.1
/SteperMotor/STEPER_DIRECTION: A1.16 (DIR), J7.3, U9.4 (Y)
/SteperMotor/STEPER_ENABLE: A1.9 (~ENABLE), J7.1, U7.4 (Y)
/SteperMotor/STEPER_STEP: A1.15 (STEP), J7.2, U8.4 (Y)
GND: A1.1 (GND), A1.7 (GND), C37.2, C38.2, C39.2, C40.2, C41.2, C42.2, C43.2, C44.2, C45.2, C46.2, C47.2, C48.2, R36.2, R38.1, R40.1, U7.3 (GND), U8.3 (GND), U9.3 (GND); also elsewhere on the board
unnamed: A1.10 (MS1), R36.1, R37.1
unnamed: A1.11 (MS2), R38.2, R39.2
unnamed: A1.12 (MS3), R40.2, R41.2
VCC: A1.8 (VMOT), C42.1, C43.1, C44.1, C45.1, C46.1, C47.1; also elsewhere on the board

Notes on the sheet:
3.3V signal to 5V
VUA680M1JTR-1010

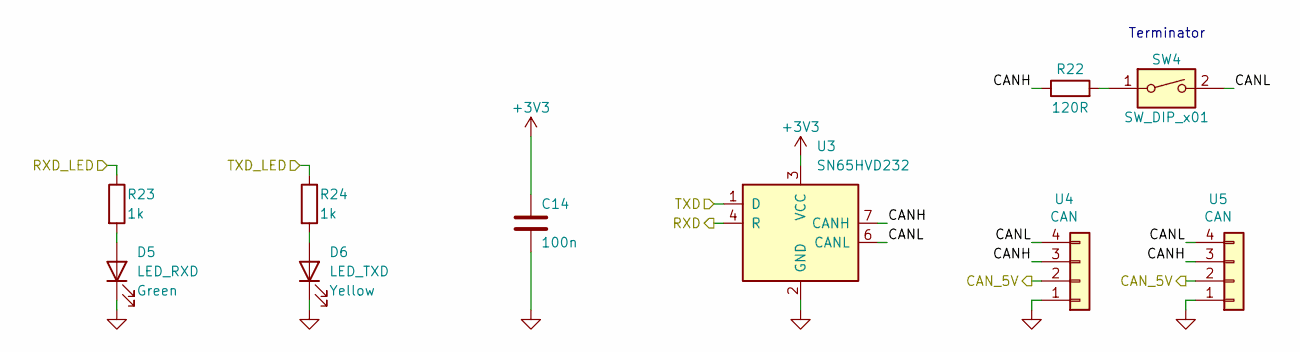
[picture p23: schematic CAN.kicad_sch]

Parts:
C14: 100n; C_0402_1005Metric
D5: LED_RXD; D_0603_1608Metric
D6: LED_TXD; D_0603_1608Metric
R22: 120R; R_0603_1608Metric
R23, R24: 1k; R_0402_1005Metric
SW4: SW_DIP_x01; SW_DIP_SPSTx01_Slide_6.7x4.1mm_W6.73mm_P2.54mm_LowProfile_J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
U3: SN65HVD232; SOIC-8_3.9x4.9mm_P1.27mm
U4, U5: CAN; Molex_Micro-Fit_3.0_43045-0412_2x02_P3.00mm_Vertical

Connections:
+3V3: C14.1, U3.3 (VCC); also elsewhere on the board
/CAN/CANH: R22.1, U3.7 (CANH), U4.3, U5.3
/CAN/CANL: SW4.2, U3.6 (CANL), U4.4, U5.4
/CAN/CAN_5V: U4.2, U5.2; also elsewhere on the board
/CAN/RXD: U3.4 (R); also elsewhere on the board
/CAN/RXD_LED: R23.1; also elsewhere on the board
/CAN/TXD: U3.1 (D); also elsewhere on the board
/CAN/TXD_LED: R24.1; also elsewhere on the board
GND: C14.2, D5.1 (K), D6.1 (K), U3.2 (GND), U4.1, U5.1; also elsewhere on the board
unnamed: D5.2 (A), R23.2
unnamed: D6.2 (A), R24.2
unnamed: R22.2, SW4.1

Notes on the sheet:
Terminator

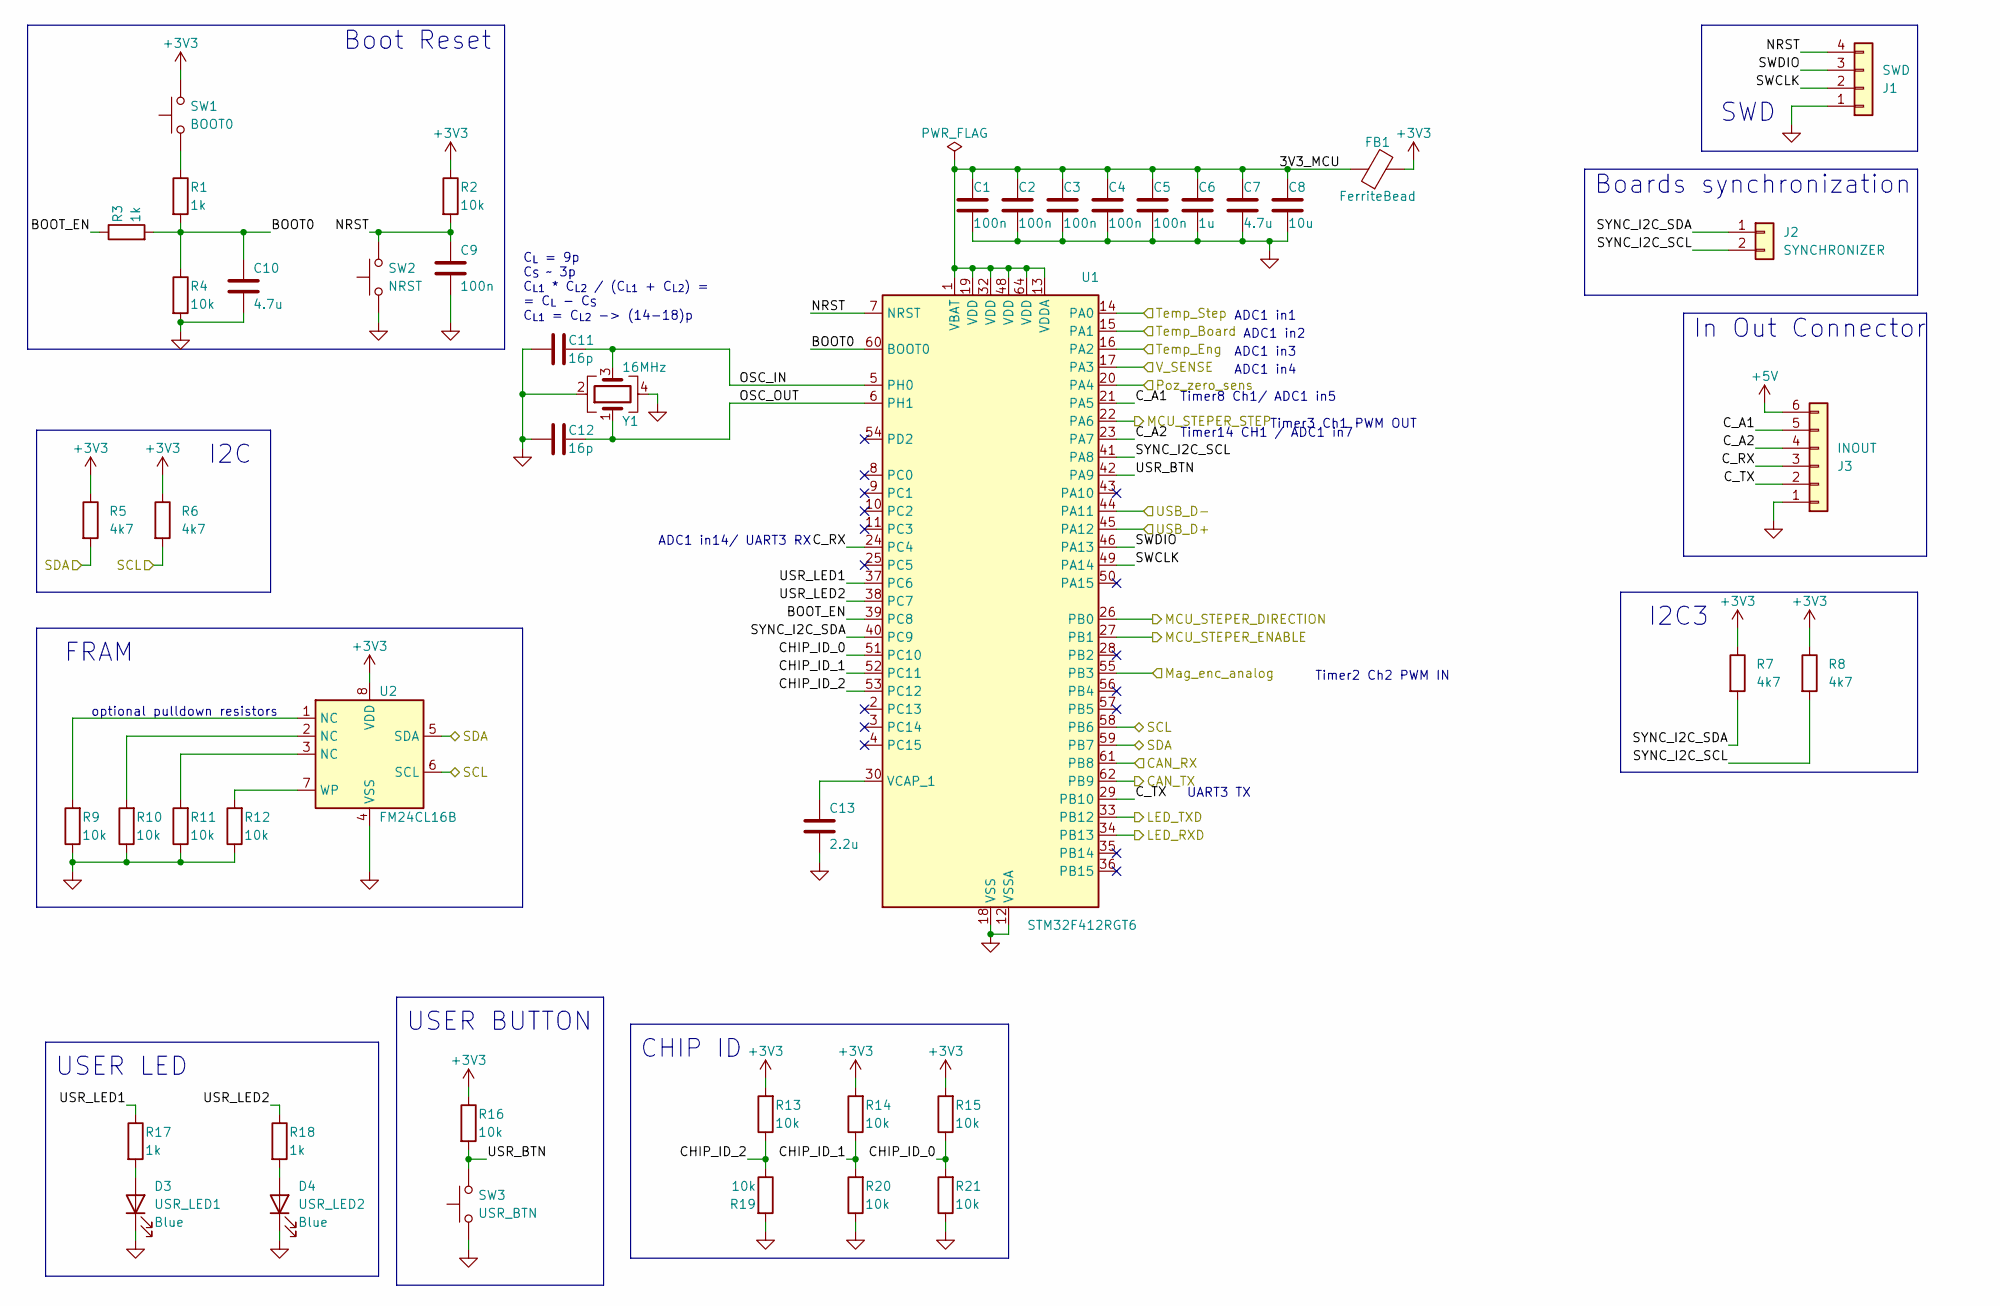
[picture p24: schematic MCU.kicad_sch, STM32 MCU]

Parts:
C1, C2, C3, C4, C5, C9: 100n; C_0402_1005Metric
C6: 1u; C_0603_1608Metric
C7: 4.7u; C_0603_1608Metric
C8: 10u; C_0805_2012Metric
C10: 4.7u; C_0402_1005Metric
C11, C12: 16p; C_0402_1005Metric
C13: 2.2u; C_0603_1608Metric
D3: USR_LED1; D_0603_1608Metric
D4: USR_LED2; D_0603_1608Metric
FB1: FerriteBead; L_0805_2012Metric
J1: SWD; PinHeader_1x04_P2.54mm_Vertical
J2: SYNCHRONIZER; JST_XH_B2B-XH-A_1x02_P2.50mm_Vertical
J3: INOUT; JST_XH_B6B-XH-A_1x06_P2.50mm_Vertical
R1, R3, R17, R18: 1k; R_0402_1005Metric
R2, R4, R9, R10, R11, R12, R13, R14, R15, R16, R19, R20, R21: 10k; R_0402_1005Metric
R5, R6, R7, R8: 4k7; R_0402_1005Metric
SW1: BOOT0; SW_SPST_PTS810
SW2: NRST; SW_SPST_PTS810
SW3: USR_BTN; SW_SPST_PTS810
U1: STM32F412RGT6; LQFP-64_10x10mm_P0.5mm
U2: FM24CL16B; SOIC-8_3.9x4.9mm_P1.27mm
Y1: 16MHz; Crystal_SMD_3225-4Pin_3.2x2.5mm

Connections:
+3V3: FB1.2, R2.1, R5.1, R6.1, R7.1, R8.1, R13.2, R14.2, R15.2, R16.1, SW1.2, U2.8 (VDD); also elsewhere on the board
+5V: J3.6; also elsewhere on the board
/CAN/RXD: U1.61 (PB8); also elsewhere on the board
/CAN/RXD_LED: U1.34 (PB13); also elsewhere on the board
/CAN/TXD: U1.62 (PB9); also elsewhere on the board
/CAN/TXD_LED: U1.33 (PB12); also elsewhere on the board
/MCU/3V3_MCU: C1.1, C2.1, C3.1, C4.1, C5.1, C6.1, C7.1, C8.1, FB1.1, U1.1 (VBAT), U1.13 (VDDA), U1.19 (VDD), U1.32 (VDD), U1.48 (VDD), U1.64 (VDD)
/MCU/BOOT0: C10.1, R1.2, R3.2, R4.1, U1.60 (BOOT0)
/MCU/BOOT_EN: R3.1, U1.39 (PC8)
/MCU/CHIP_ID_0: R15.1, R21.2, U1.51 (PC10)
/MCU/CHIP_ID_1: R14.1, R20.2, U1.52 (PC11)
/MCU/CHIP_ID_2: R13.1, R19.1, U1.53 (PC12)
/MCU/C_A1: J3.5, U1.21 (PA5)
/MCU/C_A2: J3.4, U1.23 (PA7)
/MCU/C_RX: J3.3, U1.24 (PC4)
/MCU/C_TX: J3.2, U1.29 (PB10)
/MCU/MCU_STEPER_DIRECTION: U1.26 (PB0); also elsewhere on the board
/MCU/MCU_STEPER_ENABLE: U1.27 (PB1); also elsewhere on the board
/MCU/MCU_STEPER_STEP: U1.22 (PA6); also elsewhere on the board
/MCU/Mag_enc_analog: U1.55 (PB3); also elsewhere on the board
/MCU/NRST: C9.1, J1.4, R2.2, SW2.2, U1.7 (NRST)
/MCU/OSC_IN: C11.2, U1.5 (PH0), Y1.3
/MCU/OSC_OUT: C12.2, U1.6 (PH1), Y1.1
/MCU/Poz_zero_sens: U1.20 (PA4); also elsewhere on the board
/MCU/SCL: R6.2, U1.58 (PB6), U2.6 (SCL); also elsewhere on the board
/MCU/SDA: R5.2, U1.59 (PB7), U2.5 (SDA); also elsewhere on the board
/MCU/SWCLK: J1.2, U1.49 (PA14)
/MCU/SWDIO: J1.3, U1.46 (PA13)
/MCU/SYNC_I2C_SCL: J2.2, R8.2, U1.41 (PA8)
/MCU/SYNC_I2C_SDA: J2.1, R7.2, U1.40 (PC9)
/MCU/Temp_Board: U1.15 (PA1); also elsewhere on the board
/MCU/Temp_Eng: U1.16 (PA2); also elsewhere on the board
/MCU/Temp_Step: U1.14 (PA0); also elsewhere on the board
/MCU/USB_D+: U1.45 (PA12); also elsewhere on the board
/MCU/USB_D-: U1.44 (PA11); also elsewhere on the board
/MCU/USR_BTN: R16.2, SW3.2, U1.42 (PA9)
/MCU/USR_LED1: R17.1, U1.37 (PC6)
/MCU/USR_LED2: R18.1, U1.38 (PC7)
/MCU/V_SENSE: U1.17 (PA3); also elsewhere on the board
GND: C1.2, C2.2, C3.2, C4.2, C5.2, C6.2, C7.2, C8.2, C9.2, C10.2, C11.1, C12.1, C13.2, D3.1 (K), D4.1 (K), J1.1, J3.1, R4.2, R9.1, R10.1, R11.1, R12.1, R19.2, R20.1, R21.1, SW2.1, SW3.1, U1.12 (VSSA), U1.18 (VSS), U1.31 (VSS), U1.47 (VSS), U1.63 (VSS), U2.4 (VSS), Y1.2, Y1.4; also elsewhere on the board
unnamed: D3.2 (A), R17.2
unnamed: D4.2 (A), R18.2
unnamed: R1.1, SW1.1
unnamed: R9.2, U2.1 (NC)
unnamed: R10.2, U2.2 (NC)
unnamed: R11.2, U2.3 (NC)
unnamed: C13.1, U1.30 (VCAP_1)
unnamed: R12.2, U2.7 (WP)

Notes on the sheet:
UART3 TX
FRAM
Timer2 Ch2 PWM IN
Timer3 Ch1 PWM OUT
C_{L} = 9p C_{S} ~ 3p C_{L1} * C_{L2} / (C_{L1} + C_{L2}) = = C_{L} - C_{S} C_{L1} = C_{L2} -> (14-18)p
In Out Connector
optional pulldown resistors
I2C3
Boot Reset
ADC1 in3
CHIP ID
Timer14 CH1 / ADC1 in7
SWD
USER LED
USER BUTTON
ADC1 in4
ADC1 in14/ UART3 RX
Timer8 Ch1/ ADC1 in5
ADC1 in1
ADC1 in2
I2C
Boards synchronization

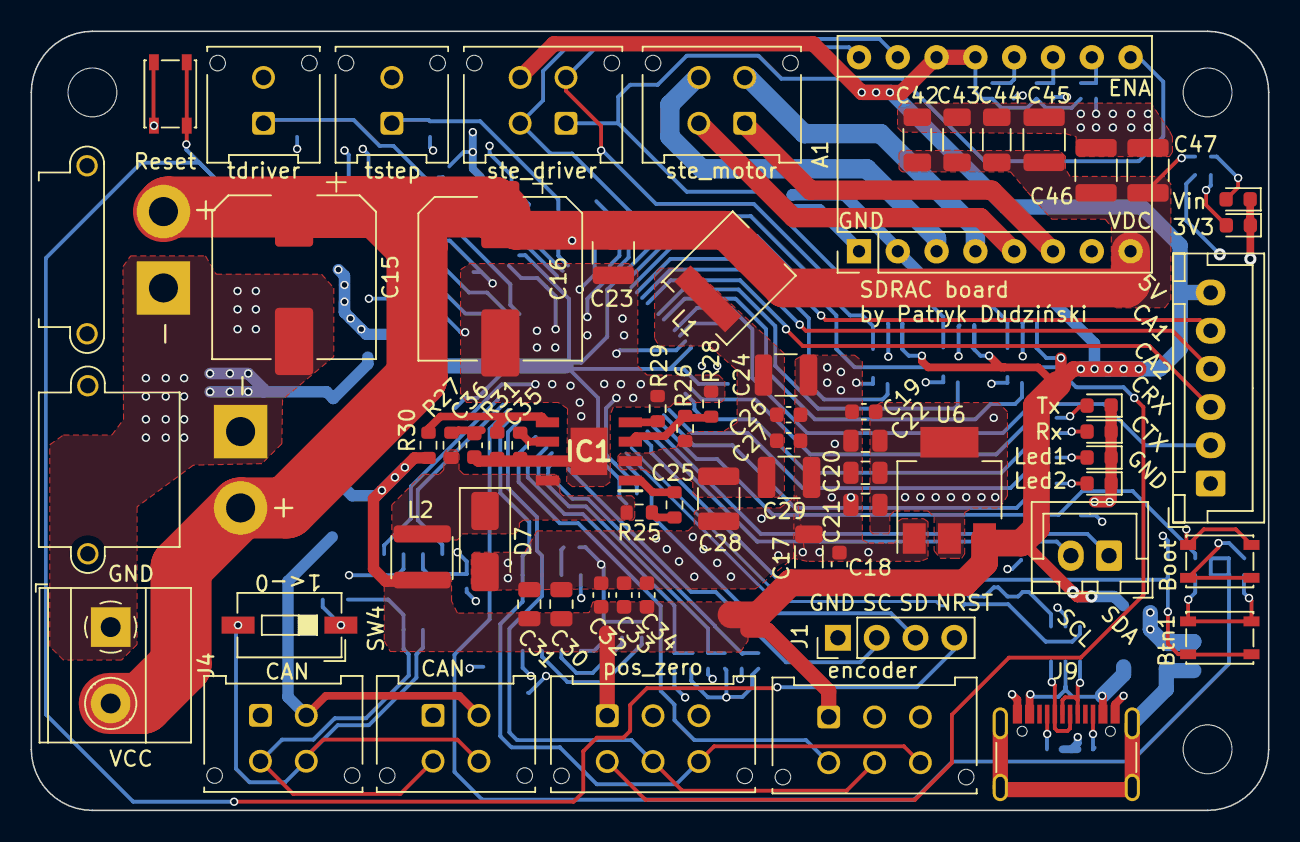
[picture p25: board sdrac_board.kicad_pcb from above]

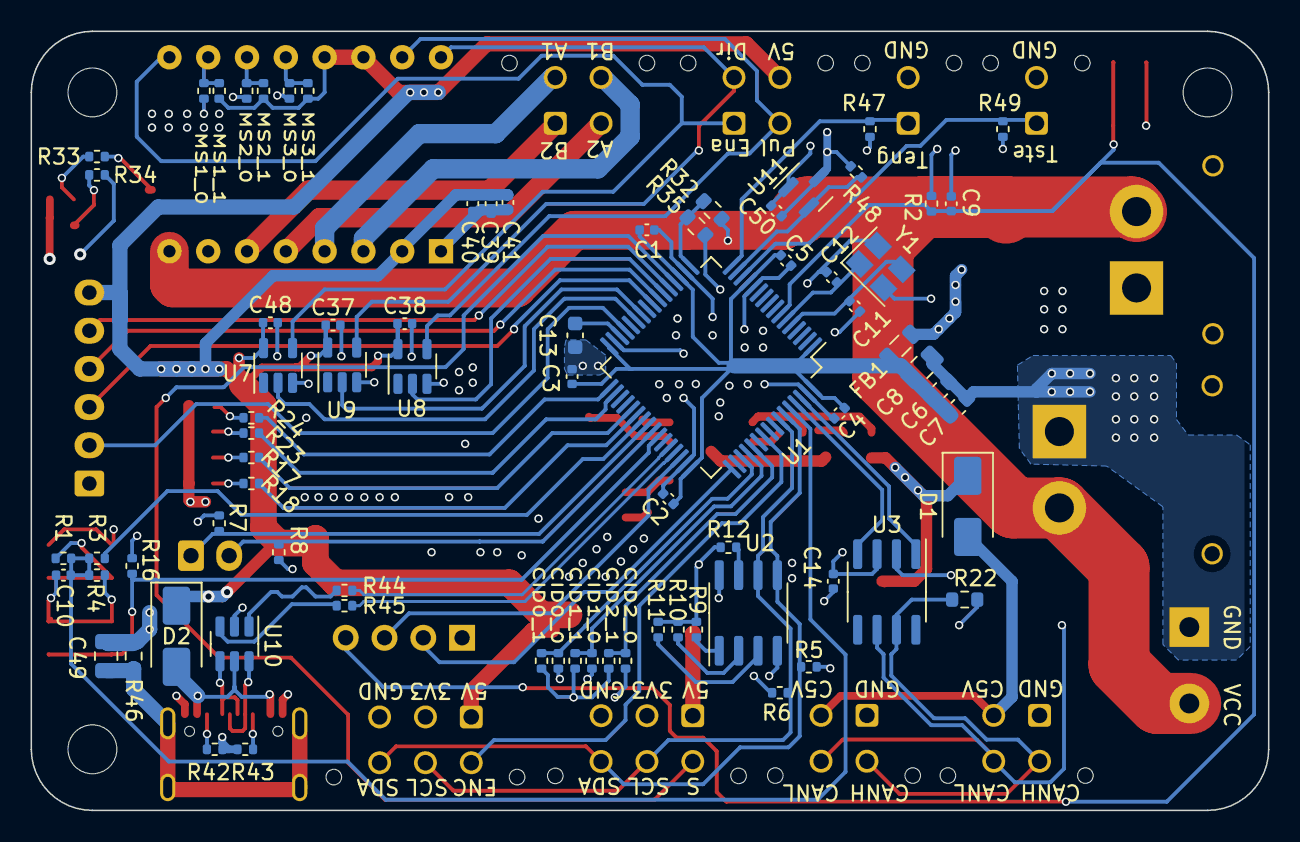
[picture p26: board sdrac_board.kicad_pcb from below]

Board: 4 copper layers, 81.0 x 51.0 mm, 145 parts (76 on the bottom side), 84 nets.

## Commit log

2024-03-08 init commit added all fiels
    [430450212.stp, 430450412.stp, 430450612.stp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]
2024-03-12 fixed caps and added nreset
    [BOM-sdrac_board.csv, MCU.kicad_sch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]
2024-03-18 addded 6pin conenctor
    [MCU.kicad_sch, sdrac_board.kicad_pcb]
2024-03-18 updated stuf
    [BOM-sdrac_board.csv, MCU.kicad_sch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]
2024-03-20 made critical changes
    [MCU.kicad_sch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]
2024-04-15 nothing done
    [MCU.kicad_sch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]
2024-04-17 added second I2C communscation lane for synchronization and added wyas to change mcirosteping with resistors
    [BOM-sdrac_board.csv, CAN.kicad_sch, MCU.kicad_sch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]
2024-04-20 added hardware address selector
    [CAN.kicad_sch, MCU.kicad_sch, Power.kicad_sch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]
2024-04-22 rozlałem i wylałem wszystko xd
    [BOM-sdrac_board.csv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]
2024-04-27 added 10A screw terminal
    [BOM-sdrac_board.csv, CAN.kicad_sch, Power.kicad_sch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]
2024-06-11 added datasheets
    [sdrac_board.kicad_pcb]
2024-06-11 fixwed resistors values
    [Power.kicad_sch, USB.kicad_sch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]
2024-06-11 added raadme
    [sb_soldering_sheet.ods, sdrac_board_bom.csv]
2025-04-23 update to kicad 9.0
    [CAN.kicad_sch, MCU.kicad_sch, Power.kicad_sch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]
